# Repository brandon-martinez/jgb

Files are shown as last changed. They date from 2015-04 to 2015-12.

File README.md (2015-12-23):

# LFEV 2015 CAN Communications Microprocessor #

This directory contains the Lafayette College Formula Electric Vehicle CAN Communications Board. This board is responsible for relaying all low level inputs and outputs (ADC, D2A, GPIO) from vehicle sub-systems to the main SCADA computer. This design contains both hardware (PCB), and the firmware written for the device.

## Hardware ##
All hardware was created in KiCad (old-stable), and is located in the 'hardware' directory. The project is described in more detail there.

## Software ##
Software written for this project is located in the 'software' directory. The target architecture for the firmware is the ATMega16M1 AVR. Software build proceedures, programming the device, and project organization are all described in more detail in the folder.

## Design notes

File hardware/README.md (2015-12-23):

# LFEV 2015 CAN Communications Microprocessor Hardware #
This directory contains the CAN communications board (JGB) designed for the spring 2015 semester.

## Overview ##
This circuit board is the primary interface between SCADA and all other systems. It is used to interface low level devices such as relays, ADCs, and other inputs/outputs to the SCADA computer via a CAN bus. This board was designed for prototyping purposes, and ensures consitant message format is used on the CAN bus. Any device which communicates via the CAN bus should inteface through this board.

The microcontroller present on this board, and the software which runs on it should eventually be integrated into each node which must communicate via the CAN bus.

## System Capabilities ##

## Target Device ##
This software is written for the **Atmel ATMEGA 16M1 Automotive AVR**  
  
This device was selected for its price, software availability, documentation and onboard CAN bus support.

1. [ATMega16M1 Overview](http://www.atmel.com/devices/atmega16m1.aspx)
2. [ATMega16M1 Datasheet](http://www.atmel.com/images/doc8209.pdf)

### Features ###

* Atmel® AVR® 8-bit microcontroller
* Up to 1 MIPS throughput per MHz
* 16KBytes flash of in-system programmable program memory
* 512B of in-system programmable EEPROM
* 1KBytes internal SRAM
* On-chip debug interface (debugWIRE)
* CAN 2.0A/B with six message objects - ISO 16845 certified
* Variable PWM duty cycle and frequency
* Synchronous update of all PWM registers
* Peripheral features
* One 8-bit general purpose timer/counter
* One 16-bit general purpose timer/counter
* One master/slave SPI serial interface
* 10-bit ADC
	* 11 single ended channels
	* Three differential ADC channel pairs (5×, 10×, 20×, 40×)
* 10-bit DAC for variable voltage reference (comparators, ADC)
* Programmable watchdog timer with separate on-chip oscillator
* On-chip temperature sensor

### Operating Specifications ###

- Operating voltage: 2.7V - 5.5V
- Extended operating temperature:
- -40°C to +85°C
- Core speed grade:
- 0 - 8MHz @ 2.7 - 4.5V
- 0 - 16MHz @ 4.5 - 5.5V

## EDA Software Suite ##

### EDA Software Suite: ###
KiCad 'old-stable' was used to design this PCB. The technical revision was KiCad (2013-may-18)-stable, run under Gentoo Linux. The source code can be found at [kicad-20130518.ebuild](https://packages.gentoo.org/package/sci-electronics/kicad)

### Component Libraries: ###
The following KiCad libraries were used in the creation of this PCB.

1. [Walter KiCad Libraries](http://smisioto.no-ip.org/elettronica/kicad/kicad-en.htm)

### Gerber Files ###
The latest GERBER files submitted for fabrication can be found in the repository under 'can-embd/hardware/gerber/' or in the BitBucket 'Downloads' page.

## Bill of Materials ##
All parts for this board were ordered through digikey, and have a DigiKey parts number (P/N) and URL associated with them in the KiCad schematic.  
  
These associations can also be viewed in the Bill of Materials (hardware/BOM.csv).  
A BOM (DigiKey ID: 2503580) has been created, which is summarized in the 'DigiKey BOM' file below. 

1. [DigiKey BOM](DigiKey_BOM.csv) This BOM contains the required DigiKey parts to build a single board.
2. [KiCad BOM](BOM.csv) This file contains a list of all components generated by KiCad.

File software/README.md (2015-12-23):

# LFEV 2015 CAN Communications Microprocessor #
This software is written for a CAN 2.0 communications board. The is a microcontroller was designed to interface all low level analog and digital sensors present on the 2015 LFEV with the main Data Acquisition Computer (SCADA). The software is capable of handling both reading and writing data.  

## Overview ##

## Target Device ##
This software is written for the **Atmel ATMEGA 16M1 Automotive AVR**  
  
This device was selected for its price, software availability, documentation and onboard CAN bus support.

The capabilities and documentation for this device can be found at:

1. [ATMega16M1 Overview](http://www.atmel.com/devices/atmega16m1.aspx)
2. [ATMega16M1 Datasheet](http://www.atmel.com/images/doc8209.pdf)

### Toolchain Information ###
**Compiler:** GCC-4.9.2 (AVR)  
**C Library:** AVR LibC  
**Downloader:** AVRDude 5.11.1  
**Programmer:** USBtinyISP  

### Toolchain Manuals ###
[GCC User Manual](https://gcc.gnu.org/onlinedocs/gcc-4.9.2/gcc/)  
[AVR LibC User Manual](http://www.nongnu.org/avr-libc/user-manual/index.html)  
[AVRDude User Manual](http://www.nongnu.org/avrdude/user-manual/avrdude.html)  
[USBtinyISP Information](https://learn.adafruit.com/usbtinyisp)  
[ATMega16M1 User Manual](http://www.atmel.com/images/doc8209.pdf)
  
### Compiler Information ###
Here is output information from the C compiler used to write all code. A standard GCC compiler with AVR target has been used. This compiler was built from source, however the latest version of this prebuilt toolchain of could be extracted from the Arduino IDE for Mac/Window/Linux if required. [Download](http://arduino.cc/en/Main/Software)

To build a GCC AVR cross compiler, insturctions can be found at: [Tutorial](http://www.nongnu.org/avr-libc/user-manual/install_tools.html)

**Compiler Details**
```
user@scada:~/$ avr-gcc -v

Using built-in specs.
COLLECT_GCC=avr-gcc
COLLECT_LTO_WRAPPER=/usr/local/bin/../libexec/gcc/avr/4.9.2/lto-wrapper
Target: avr
Configured with: ../gcc-4.9.2/configure --prefix=/home/scada/avr-gcc/ --target=avr --enable-languages=c,c++ --disable-nls --disable-libssp --with-dwarf2
Thread model: single
gcc version 4.9.2 (GCC)

```

## Building The Software ##

This command will build the firmware image, and upload it to the target device using 'avrdude'. 
```
make
```
This makefile was configured to run with the usbTinyISP AVR programmer.   
If you are not using a usbTinyISP programmer, you will need to change the following to match your programmer.  
```
vi Makefile
```

and modify the following line

```
PGRMR={your programmer}
```

See AVRDude User Manual above for a list of supported programmers.

## Programming The Microcontroller##
**To build the firmware image only:**  
```
make build
```
**To upload the last built firmware only:**  
```
make program
```

## Configuring the Onboard Crystal Oscillator##
This command must be run to configure the AVR device upon its first program. Once this command is issued, it should not need to be run again.  

The command below configures the device to use the proper clock source (16MHz crystal) instead of the internal oscillator.
```
make fuse
```
*NOTE: This command will throw a Device ID mis-match, this is normal. This is because the ATMEGA16M1 is present listed in the AVRDude list of devices*

can_drv.h/c
can_lib.h/c

Found at:
https://eewiki.net/display/microcontroller/CAN+Example+-+ATmega32M1+-+STK600

modified to compile w/ avr-gcc

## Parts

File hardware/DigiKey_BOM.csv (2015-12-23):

Digi-Key Part Number | Manufacturer | Manufacturer Part Number | Customer Reference | Quantity 1 | Quantity 2 | Quantity 3 | Mfg Std Lead Time | Description | Comments | RoHS Status | Lead Free Status | REACH Status
490-1403-1-ND | MURATA ELECTRONICS (VA) | GRM1885C1H100JA01D |  | 2 | 0 | 0 | 18 Weeks | CAP CER 10PF 50V 5% NP0 0603 | Alternate Packaging Exists | RoHS Compliant | Lead free | Unaffected Jul-2011
3M15451-ND | 3M | 30306-6002HB |  | 1 | 0 | 0 | 6 Weeks | CONN HEADER 6POS DL STR GOLD |  | RoHS Compliant | Lead free | Not Available
401-1427-1-ND | C&K COMPONENTS (VA) | KMR221GLFS |  | 1 | 0 | 0 | 8 Weeks | SWITCH TACTILE SPST-NO 0.05A 32V | Alternate Packaging Exists | RoHS Compliant | Lead free | Unaffected Jun-2013
490-1524-1-ND | MURATA ELECTRONICS (VA) | GRM188R71E104KA01D |  | 5 | 0 | 0 | 10 Weeks | CAP CER 0.1UF 25V 10% X7R 0603 | Alternate Packaging Exists | RoHS Compliant | Lead free | Unaffected Jul-2011
609-4613-1-ND | FCI (VA) | 10118192-0001LF |  | 1 | 0 | 0 | 10 Weeks | CONN USB MICRO B RECPT SMT R/A | Alternate Packaging Exists | RoHS Compliant | Lead free | Unaffected Dec-2012
644-1037-1-ND | NDK (VA) | NX5032GA-16.000000MHZ-LN-CD-1 |  | 1 | 0 | 0 | 8 Weeks | CRYSTAL 16.0000MHZ 8PF SMD | Alternate Packaging Exists | RoHS Compliant | Lead free by exemption | Unaffected Dec-2014
732-4971-1-ND | WURTH ELECTRONICS INC (VA) | 150060GS75000 |  | 3 | 0 | 0 | 8 Weeks | WL-SMCW SMD CHIP LED WATERCLEAR | Alternate Packaging Exists | RoHS Compliant | Lead free | Unaffected Jun-2012
732-4978-1-ND | WURTH ELECTRONICS INC (VA) | 150060RS75000 |  | 2 | 0 | 0 | 8 Weeks | WL-SMCW SMD CHIP LED WATERCLEAR | Alternate Packaging Exists | RoHS Compliant | Lead free | Unaffected Jun-2012
732-4981-1-ND | WURTH ELECTRONICS INC (VA) | 150060YS75000 |  | 2 | 0 | 0 | 8 Weeks | WL-SMCW SMD CHIP LED WATERCLEAR | Alternate Packaging Exists | RoHS Compliant | Lead free | Unaffected Jun-2012
732-4982-1-ND | WURTH ELECTRONICS INC (VA) | 150080BS75000 |  | 1 | 0 | 0 | 8 Weeks | WL-SMCW SMD CHIP LED WATERCLEAR | Alternate Packaging Exists | RoHS Compliant | Lead free | Unaffected Jun-2012
768-1007-1-ND | FTDI (VA) | FT232RL-REEL |  | 1 | 0 | 0 | 8-12 Weeks | IC USB FS SERIAL UART 28-SSOP | Alternate Packaging Exists | RoHS Compliant | Lead free | Unaffected Jun-2011
952-2264-ND | HARWIN INC | M20-9990346 |  | 1 | 0 | 0 | 6 Weeks | SIL VERTICAL PC TAIL PIN HEADER |  | RoHS Compliant | Lead free | Unaffected Dec-2014
ATMEGA16M1-15AZCT-ND | ATMEL (VA) | ATMEGA16M1-15AZ |  | 1 | 0 | 0 | 6 Weeks | IC MCU 8BIT 16KB FLASH 32TQFP | No delivery date available | RoHS Compliant | Lead free | Unaffected Dec-2013
ED2609-ND | ON SHORE TECHNOLOGY INC | OSTTC022162 |  | 5 | 0 | 0 | 8 Weeks | TERM BLOCK 5.08MM VERT 2POS PCB |  | RoHS Compliant | Lead free | Unaffected Dec-2014
ED2615-ND | ON SHORE TECHNOLOGY INC | OSTTC082162 |  | 3 | 0 | 0 | 8 Weeks | TERM BLOCK 5.08MM VERT 8POS PCB |  | RoHS Compliant | Lead free | Unaffected Dec-2014
MCP2551T-E/SNCT-ND | MICROCHIP TECHNOLOGY (VA) | MCP2551T-E/SN |  | 1 | 0 | 0 | 12 Weeks | IC TRANSCEIVER CAN HI-SPD 8-SOIC | Alternate Packaging Exists | RoHS Compliant | Lead free | Unaffected Dec-2014
NCP1117ST50T3GOSCT-ND | ON SEMICONDUCTOR (VA) | NCP1117ST50T3G |  | 1 | 0 | 0 | 9 Weeks | IC REG LDO 5V 1A SOT223 | Alternate Packaging Exists | RoHS Compliant | Lead free | Unaffected Dec-2014
PCE5005CT-ND | PANASONIC ELECTRONIC COMPONENTS (VA) | EEE-FT1E470AR |  | 2 | 0 | 0 | 20 Weeks | CAP ALUM 47UF 25V 20% SMD | Alternate Packaging Exists | RoHS Compliant | Lead free | Not Available
RHM1.0KCGCT-ND | ROHM SEMICONDUCTOR (PASSIVE) (VA) | MCR03ERTJ102 |  | 10 | 0 | 0 | 6-8 Weeks | RES SMD 1K OHM 5% 1/10W 0603 | Alternate Packaging Exists | RoHS Compliant | Lead free | Unaffected Jun-2012
RHM10KCGCT-ND | ROHM SEMICONDUCTOR (PASSIVE) (VA) | MCR03ERTJ103 |  | 2 | 0 | 0 | 6-8 Weeks | RES SMD 10K OHM 5% 1/10W 0603 | Alternate Packaging Exists | RoHS Compliant | Lead free | Unaffected Jun-2012
RHM220CGCT-ND | ROHM SEMICONDUCTOR (PASSIVE) (VA) | MCR03ERTJ221 |  | 4 | 0 | 0 | 6-8 Weeks | RES SMD 220 OHM 5% 1/10W 0603 | Alternate Packaging Exists | RoHS Compliant | Lead free | Not Available
SK310A-LTPMSCT-ND | MICRO COMMERCIAL CO (VA) | SK310A-LTP |  | 3 | 0 | 0 | 8-12 Weeks | DIODE SCHOTTKY 100V 3A DO214AC | Alternate Packaging Exists | RoHS Compliant | Lead free | Unaffected Dec-2014
VO14642AABCT-ND | VISHAY SEMICONDUCTOR OPTO DIVISION (VA) | VO14642AABTR |  | 3 | 0 | 0 | 4 Weeks | RELAY SSR SPST-NO 2A 60V 6SMD | Alternate Packaging Exists | RoHS Compliant | Lead free | Unaffected Jun-2014

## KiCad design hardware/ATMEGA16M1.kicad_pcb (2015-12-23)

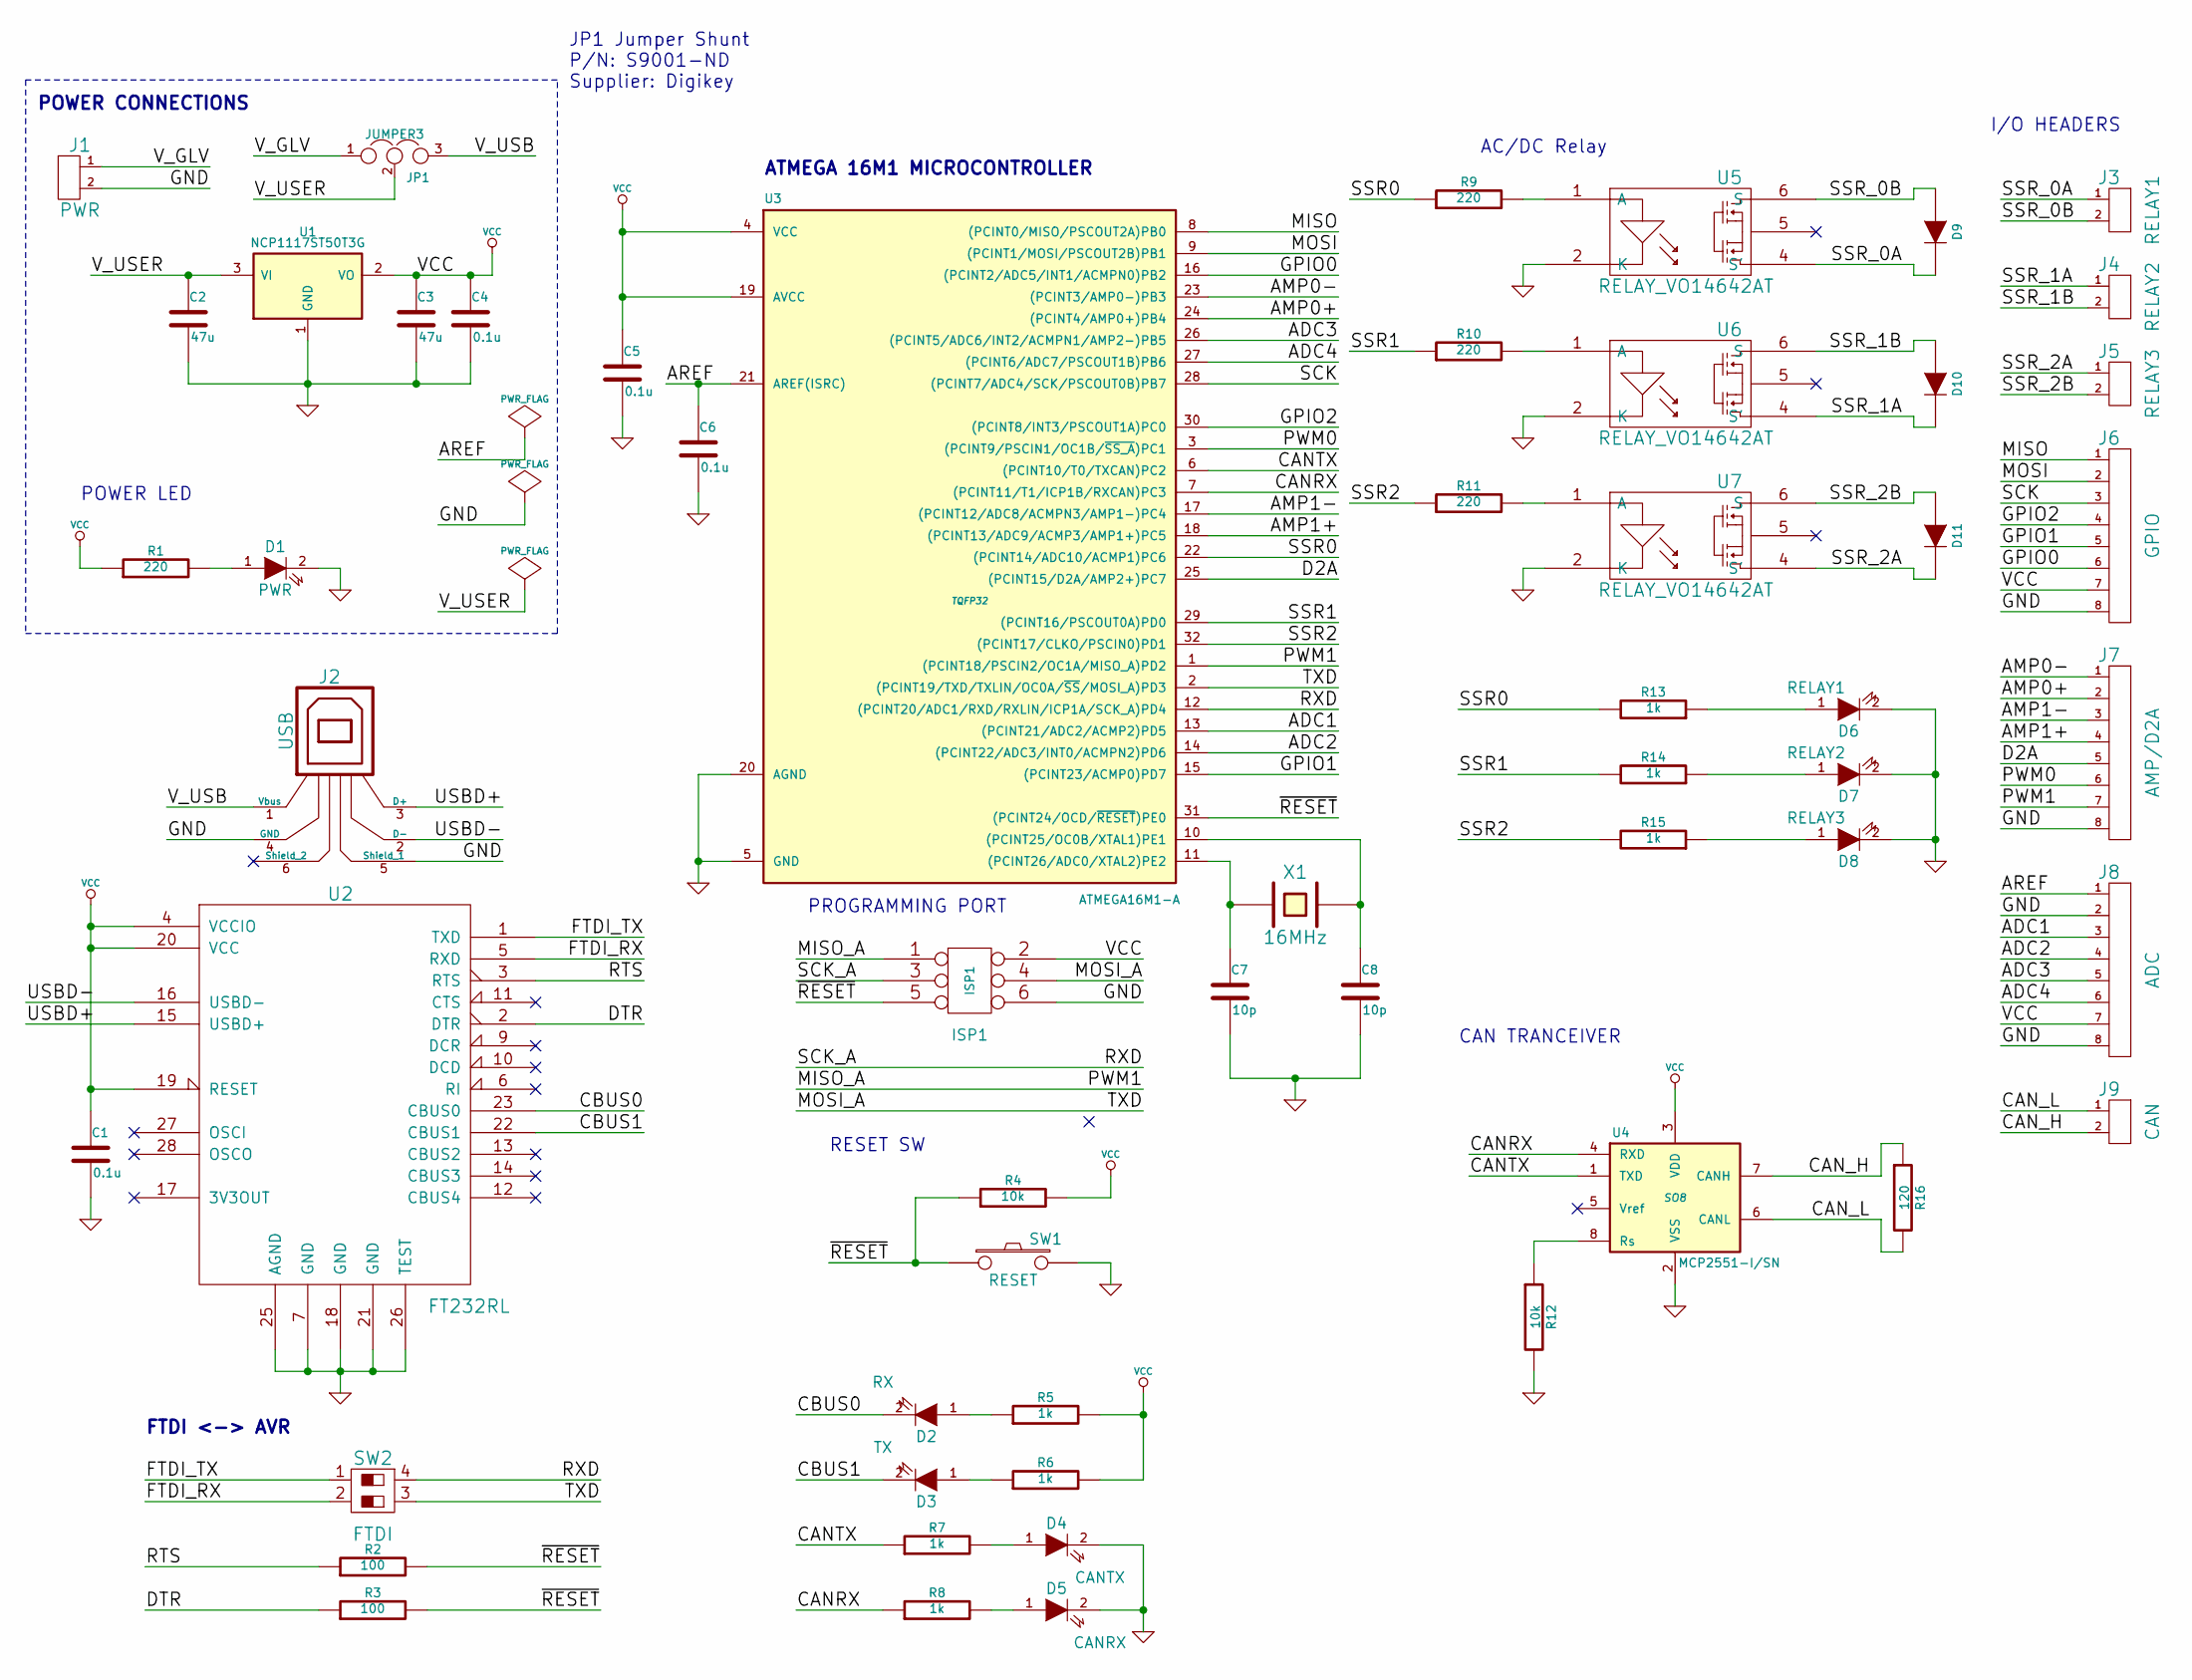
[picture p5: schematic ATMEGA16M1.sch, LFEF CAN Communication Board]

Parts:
C1, C4, C5, C6: 0.1u
C2, C3: 47u
C7, C8: 10p
D1: PWR
D2: RX
D3: TX
D4: CANTX
D5: CANRX
D6: RELAY1
D7: RELAY2
D8: RELAY3
D9, D10, D11: DIODE
ISP1: ISP1
J1: PWR
J2: USB
J3: RELAY1
J4: RELAY2
J5: RELAY3
J6: GPIO
J7: AMP/D2A
J8: ADC
J9: CAN
JP1: JUMPER3
R1, R9, R10, R11: 220
R2, R3: 100
R4, R12: 10k
R5, R6, R7, R8, R13, R14, R15: 1k
R16: 120
SW1: RESET
SW2: FTDI
U1: NCP1117ST50T3G
U2: FT232RL
U3: ATMEGA16M1-A; TQFP32
U4: MCP2551-I/SN; SO8
U5, U6, U7: RELAY_VO14642AT
X1: 16MHz

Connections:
/ADC1: J8.3, U3.13 ((PCINT21/ADC2/ACMP2)PD5)
/ADC2: J8.4, U3.14 ((PCINT22/ADC3/INT0/ACMPN2)PD6)
/ADC3: J8.5, U3.26 ((PCINT5/ADC6/INT2/ACMPN1/AMP2-)PB5)
/ADC4: J8.6, U3.27 ((PCINT6/ADC7/PSCOUT1B)PB6)
/AMP0+: J7.2, U3.24 ((PCINT4/AMP0+)PB4)
/AMP0-: J7.1, U3.23 ((PCINT3/AMP0-)PB3)
/AMP1+: J7.4, U3.18 ((PCINT13/ADC9/ACMP3/AMP1+)PC5)
/AMP1-: J7.3, U3.17 ((PCINT12/ADC8/ACMPN3/AMP1-)PC4)
/AREF: C6.1, J8.1, U3.21 (AREF(ISRC))
/CANRX: R8.1, U3.7 ((PCINT11/T1/ICP1B/RXCAN)PC3), U4.4 (RXD)
/CANTX: R7.1, U3.6 ((PCINT10/T0/TXCAN)PC2), U4.1 (TXD)
/CAN_H: J9.2, R16.1, U4.7 (CANH)
/CAN_L: J9.1, R16.2, U4.6 (CANL)
/CBUS0: D2.2 (K), U2.23 (CBUS0)
/CBUS1: D3.2 (K), U2.22 (CBUS1)
/D2A: J7.5, U3.25 ((PCINT15/D2A/AMP2+)PC7)
/DTR: R3.1, U2.2 (DTR)
/FTDI_RX: SW2.2, U2.5 (RXD)
/FTDI_TX: SW2.1, U2.1 (TXD)
/GPIO0: J6.6, U3.16 ((PCINT2/ADC5/INT1/ACMPN0)PB2)
/GPIO1: J6.5, U3.15 ((PCINT23/ACMP0)PD7)
/GPIO2: J6.4, U3.30 ((PCINT8/INT3/PSCOUT1A)PC0)
/MISO: J6.1, U3.8 ((PCINT0/MISO/PSCOUT2A)PB0)
/MISO_A: ISP1.1, J7.7, U3.1 ((PCINT18/PSCIN2/OC1A/MISO_A)PD2)
/MOSI: J6.2, U3.9 ((PCINT1/MOSI/PSCOUT2B)PB1)
/MOSI_A: ISP1.4, SW2.3, U3.2 ((PCINT19/TXD/TXLIN/OC0A/~SS~/MOSI_A)PD3)
/PWM0: J7.6, U3.3 ((PCINT9/PSCIN1/OC1B/~SS_A~)PC1)
/RTS: R2.1, U2.3 (RTS)
/RXD: ISP1.3, SW2.4, U3.12 ((PCINT20/ADC1/RXD/RXLIN/ICP1A/SCK_A)PD4)
/SCK: J6.3, U3.28 ((PCINT7/ADC4/SCK/PSCOUT0B)PB7)
/SSR0: R9.1, R13.2, U3.22 ((PCINT14/ADC10/ACMP1)PC6)
/SSR1: R10.1, R14.2, U3.29 ((PCINT16/PSCOUT0A)PD0)
/SSR2: R11.1, R15.2, U3.32 ((PCINT17/CLKO/PSCIN0)PD1)
/SSR_0A: D9.2 (K), J3.1, U5.4 (S')
/SSR_0B: D9.1 (A), J3.2, U5.6 (S)
/SSR_1A: D10.2 (K), J4.1, U6.4 (S')
/SSR_1B: D10.1 (A), J4.2, U6.6 (S)
/SSR_2A: D11.2 (K), J5.1, U7.4 (S')
/SSR_2B: D11.1 (A), J5.2, U7.6 (S)
/USBD+: J2.3 (D+), U2.15 (USBD+)
/USBD-: J2.2 (D-), U2.16 (USBD-)
/V_GLV: J1.1, JP1.1
/V_USB: J2.1 (Vbus), JP1.3
/V_USER: C2.1, JP1.2, U1.3 (VI)
/~RESET: ISP1.5, R2.2, R3.2, R4.1, SW1.1, U3.31 ((PCINT24/OCD/~RESET~)PE0)
GND: C1.2, C2.2, C3.2, C4.2, C5.2, C6.2, C7.2, C8.2, D1.2 (K), D4.2 (K), D5.2 (K), D6.2 (K), D7.2 (K), D8.2 (K), ISP1.6, J1.2, J2.4 (GND), J2.5 (Shield_1), J6.8, J7.8, J8.2, J8.8, R12.2, SW1.2, U1.1 (GND), U2.7 (GND), U2.18 (GND), U2.21 (GND), U2.25 (AGND), U2.26 (TEST), U3.5 (GND), U3.20 (AGND), U4.2 (VSS), U5.2 (K), U6.2 (K), U7.2 (K)
unnamed: R12.1, U4.8 (Rs)
unnamed: D7.1 (A), R14.1
unnamed: D3.1 (A), R6.1
unnamed: R11.2, U7.1 (A)
unnamed: R9.2, U5.1 (A)
unnamed: R10.2, U6.1 (A)
unnamed: D6.1 (A), R13.1
unnamed: D8.1 (A), R15.1
unnamed: D1.1 (A), R1.2
unnamed: D2.1 (A), R5.1
unnamed: D4.1 (A), R7.2
unnamed: D5.1 (A), R8.2
unnamed: C7.1, U3.11 ((PCINT26/ADC0/XTAL2)PE2), X1.1
unnamed: C8.1, U3.10 ((PCINT25/OC0B/XTAL1)PE1), X1.2
VCC: C1.1, C3.1, C4.1, C5.1, ISP1.2, J6.7, J8.7, R1.1, R4.2, R5.2, R6.2, U1.2 (VO), U2.4 (VCCIO), U2.19 (RESET), U2.20 (VCC), U3.4 (VCC), U3.19 (AVCC), U4.3 (VDD)

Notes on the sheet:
POWER CONNECTIONS
FTDI <-> AVR
ATMEGA 16M1 MICROCONTROLLER
AC/DC Relay
RESET SW
PROGRAMMING PORT
CAN TRANCEIVER
I/O HEADERS
POWER LED
JP1 Jumper Shunt P/N: S9001-ND Supplier: Digikey

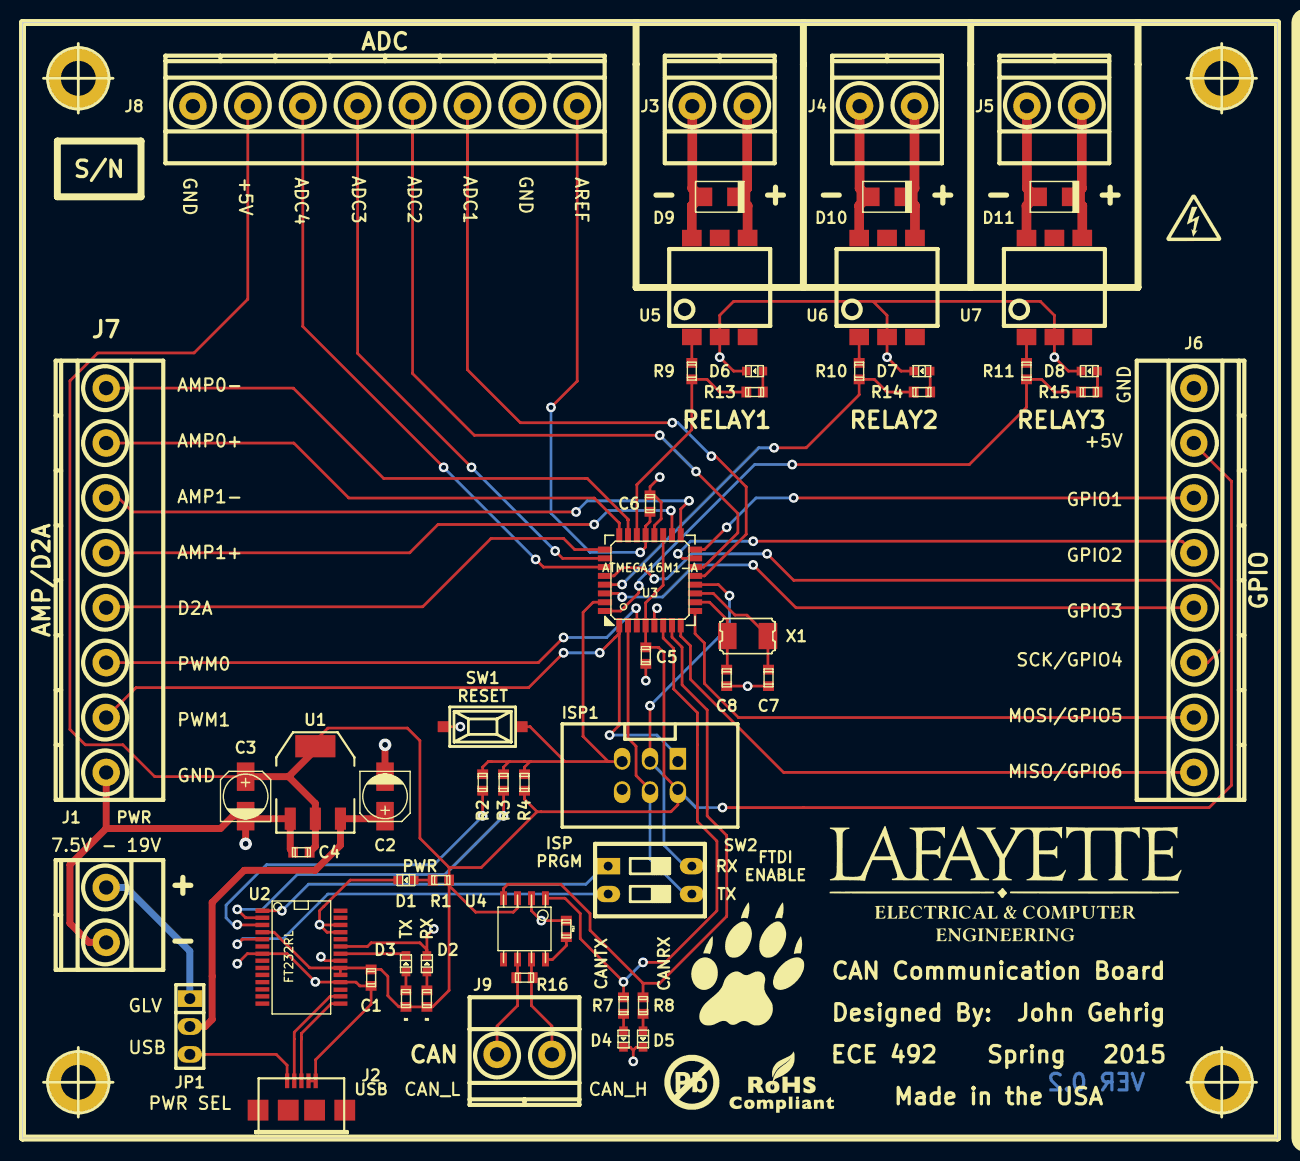
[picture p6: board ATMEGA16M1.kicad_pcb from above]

Board: 2 copper layers, 114.3 x 101.6 mm, 60 parts (0 on the bottom side), 61 nets.

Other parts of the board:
hole_5mm, hole_5mm#2, hole_5mm#3, hole_5mm#4: VAL**; hole_5mm

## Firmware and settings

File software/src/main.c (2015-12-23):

#include "config.h"

//AVR-LIBC Headers 
#include <avr/cpufunc.h>
#include <avr/interrupt.h>
#include <avr/io.h>
#include <avr/sleep.h>

#include <util/delay.h>

#include <stdio.h>

#include "can_lib.h"
#include "adc.h"
#include "timer.h"
#include "uart.h"

//Device CAN_ID
#define CAN_ID  0x080
#define CAN_MSK ~(0x03) 

//uint8_t response_data[CAN_BUFFER_SIZE];
uint8_t can_buffer_tx[CAN_BUFFER_SIZE];
uint8_t can_buffer_rx[CAN_BUFFER_SIZE];

void setup(void) {
	analog_setup(ADC_AVCC, ADC_SCALE_128);

	uart_init(BAUD);
	
	can_init(0);
	
	fdevopen(&uart_putc, NULL);
	fdevopen(&uart_getc, NULL);
	
	sei();
}

int main(void) {
	st_cmd_t tx_msg;
	st_cmd_t rx_msg;
	//Setup Comment
	setup();
	char str [] = "Hello World?\n";
	for(;;) {
		puts(str);
		//adc_1
		//uart_println(adc_read(2));
		////adc_2
		//uart_println(adc_read(3));
		////adc_3
		//uart_println(adc_read(6));
		////adc_4
		//uart_println(adc_read(7));
		////amp_0
		//uart_println(adc_read(15));
		////amp_1
		//uart_println(adc_read(16));
		
		_delay_ms(2000);
	}
	
	
	////point message object to first element of data buffer
	//tx_msg.pt_data = &tx_buffer[0];
	////standard CAN frame type (2.0A)
	//tx_msg.ctrl.ide = 0;
	////Number of bytes being sent (8 max)
	//tx_msg.dlc = CAN_BUFFER_SIZE;
	////populate ID field with ID Tag
	//tx_msg.id.std = CAN_ID;
	////assign this as a "Standard (2.0A) Reply" message object
	//tx_msg.cmd = CMD_TX_DATA;

	////wait for MOb to configure
    //while(can_cmd(&tx_msg) != CAN_CMD_ACCEPTED);

    //// send a response
    //while(can_get_status(&tx_msg) == CAN_STATUS_NOT_COMPLETED);
    //_delay_ms(1000);
	
	return 0;
}

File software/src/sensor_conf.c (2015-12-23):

#include "sensor_conf.h"

#include <avr/eeprom.h>

void setup_io(struct sys_config *sys) {
	DDRA = 0; 
	DDRB = 0;
	DDRC = 0;
	DDRD = 0;
	
	//ADC1
	sys->adc_1->en = 0;
	sys->adc_1->ddr = 0;
	sys->adc_1->slot = 0;
	sys->adc_1->frame = 0;
	sys->adc_1->get_value = 0;
	
	
	//ADC2
	sys->adc_2->en = 0;
	sys->adc_2->ddr = 0;
	sys->adc_2->slot = 0;
	sys->adc_2->frame = 0;
	sys->adc_1->get_value = 0;
	
	//ADC3
	sys->adc_3->en = 0;
	sys->adc_3->ddr = 0;
	sys->adc_3->slot = 0;
	sys->adc_3->frame = 0;
	sys->adc_1->get_value = 0;
	
	//ADC4
	sys->adc_4;
	sys->adc_4->en = 0;
	sys->adc_4->ddr = 0;
	sys->adc_4->slot = 0;
	sys->adc_4->frame = 0;
	sys->adc_1->get_value = 0;
	
	//AMP0
	sys->amp_0->en = 0;
	sys->amp_0->ddr = 0;
	sys->amp_0->slot = 0;
	sys->amp_0->frame = 0;
	
	//AMP1
	sys->amp_1->en = 0;
	sys->amp_1->ddr = 0;
	sys->amp_1->slot = 0;
	sys->amp_1->frame = 0;
	
	//D2A
	sys->d2a;
	sys->d2a->en = 0;
	sys->d2a->ddr = 0;
	sys->d2a->slot = 0;
	sys->d2a->frame = 0;
	DDRC |= (1 << PC7);
	
	//PWM0
	sys->pwm_0->en = 0;
	sys->pwm_0->ddr = 0;
	sys->pwm_0->slot = 0;
	sys->pwm_0->frame = 0;
	DDRC |= (1 << PC1);
	
	//PWM1
	sys->pwm_1->en = 0;
	sys->pwm_1->ddr = 0;
	sys->pwm_1->slot = 0;
	sys->pwm_1->frame = 0;
	DDRD |= (1 << PD2);
	
	//SSR0
	sys->ssr_0->en = 0;
	sys->ssr_0->ddr = 0;
	sys->ssr_0->slot = 0;
	sys->ssr_0->frame = 0;
	DDRC |= (1 << PC6);
	
	//SSR1
	sys->ssr_1->en = 0;
	sys->ssr_1->ddr = 0;
	sys->ssr_1->slot = 0;
	sys->ssr_1->frame = 0;
	DDRC |= (1 << PD0);
	
	//SSR2
	sys->ssr_2->en = 0;
	sys->ssr_2->ddr = 0;
	sys->ssr_2->slot = 0;
	sys->ssr_2->frame = 0;
	DDRC |= (1 << PD1);
}

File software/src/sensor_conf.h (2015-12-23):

#ifndef SENSOR_CONF_H
#define SENSOR_CONF_H

//GPIO
const  uint8_t GPIO0_BIT  = PB2;
const *uint8_t GPIO0_PIN  = PINB;
const *uint8_t GPIO0_PORT = PORTB;
const *uint8_t GPIO0_DDR  = DDRB;

const  uint8_t GPIO1_BIT  = PD7;
const *uint8_t GPIO1_PIN  = &PIND;
const *uint8_t GPIO1_PORT = &PORTD;
const *uint8_t GPIO1_DDR  = &DDRD;

const  uint8_t GPIO2_BIT  = PC0;
const *uint8_t GPIO2_PIN  = &PINC;
const *uint8_t GPIO2_PORT = &PORTC;
const *uint8_t GPIO2_DDR  = &DDRC;

const  uint8_t GPIO3_BIT  = PB7;
const *uint8_t GPIO3_PIN  = &PINB;
const *uint8_t GPIO3_PORT = &PORTB;
const *uint8_t GPIO3_DDR  = &DDRB;

const  uint8_t GPIO4_BIT  = PB1;
const *uint8_t GPIO4_PIN  = &PINB;
const *uint8_t GPIO4_PORT = &PORTB;
const *uint8_t GPIO4_DDR  = &DDRB;

const  uint8_t GPIO5_BIT  = PB0;
const *uint8_t GPIO5_PIN  = &PINB;
const *uint8_t GPIO5_PORT = &PORTB;
const *uint8_t GPIO5_DDR  = &DDRB;

struct in_config {
	uint8_t en : 1;
	uint8_t slot : 2;
	uint8_t frame: 3;
	uint16_t (*get_value)(void);
};

struct out_config {
	uint8_t en : 1;
	uint8_t slot : 2;
	uint8_t frame: 3;
	void (*set_value)(uint8_t);
};

struct bit_config {
	uint8_t en : 1;
	uint8_t ddr : 1;
	uint8_t bit : 4;
	uint8_t slot : 2;
	uint8_t frame: 3;
	*uint8_t pin;
	*uint8_t port;
	*uint8_t ddr;
	void (*set_value)(uint8_t);
	uint8_t (*get_value)(void);
};

struct sys_config {
	in_config adc_1;
	in_config adc_2;
	in_config adc_3;
	in_config adc_4;
	in_config amp_0;
	in_config amp_1;
	in_config amp_1;

	out_config d2a;
	out_config pwm_0;
	out_config pwm_1;
	out_config ssr_0;
	out_config ssr_1;
	out_config ssr_2;
	
	bit_config gpio0;
	bit_config gpio1;
	bit_config gpio2;
	bit_config gpio3;
	bit_config gpio4;
	bit_config gpio5;
};

//Setup pin directions, etc
void setup_io(struct *sys_config);


#endif

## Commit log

2015-03-11 CAN Comm Board Hardware/Software Initial Commit
    [ATMEGA16M1.kicad_pcb, ATMEGA16M1.sch]
2015-03-23 PCB revisions: schematic update, cvpcb, pcb component grouping
    [ATMEGA16M1.kicad_pcb, ATMEGA16M1.sch]
2015-03-23 CAN software library added (untested), LIN UART code writtein (untested)
2015-03-24 PWM library implemented for timer0
2015-03-26 **CAN DEMONSTRATION** A working demonstration of the CAN system capable of both sending and receivng packets. ID=80
    1) cansend [interface] 80#R
    [packet count] [ADC7] [ADC7] 33 44 55 66 77
    2) cansend [interface] 80#{00-FF}
    Sets LED (pin 2) to PWM value of can packet
2015-03-28 PCB rough initial layout
    [ATMEGA16M1.kicad_pcb, ATMEGA16M1.sch]
2015-03-29 PCB physical layout (mostly) complete
    [ATMEGA16M1.kicad_pcb, ATMEGA16M1.sch]
2015-04-01 PCB Prototype Finalized, GERBERs Created, Sent for Fabrication
    [ATMEGA16M1-B_Cu.gbl, ATMEGA16M1-B_Mask.gbs, ATMEGA16M1-B_SilkS.gbo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]
2015-04-01 GERBER MODIFICATION (Annular Ring 5mil -> 10mil)
    [ATMEGA16M1-B_Cu.gbl, ATMEGA16M1-B_Mask.gbs, ATMEGA16M1-B_SilkS.gbo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]
2015-04-01 GERBER Files Panelized (Sent for Fabrication)
    [ATMEGA16M1-B_Cu.gbl, ATMEGA16M1-B_Mask.gbs, ATMEGA16M1-B_SilkS.gbo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]
2015-04-02 BOM added & schematic updated with Digikey P/N's
    [ATMEGA16M1.sch, BOM.csv]
2015-04-07 JGB documentation revisions
    [DigiKey_BOM.csv]
2015-04-11 FTDI <-> ISP issue addressed, dip switch added
    [ATMEGA16M1.kicad_pcb, ATMEGA16M1.sch]
2015-04-11 Reference designations updated, BOM.csv reflects changes & RTS DTR added
    [ATMEGA16M1.kicad_pcb, ATMEGA16M1.sch, BOM.csv]
2015-04-19 uart code, makefile updates, can_frame, test code updates
2015-04-19 CAN frame library created
2015-04-20 gerbers (ver 0.2) sent for fabrication
    [ATMEGA16M1-B_Cu.gbl, ATMEGA16M1-B_Mask.gbs, ATMEGA16M1-B_SilkS.gbo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]
2015-04-21 printf implemented, working on scanf
